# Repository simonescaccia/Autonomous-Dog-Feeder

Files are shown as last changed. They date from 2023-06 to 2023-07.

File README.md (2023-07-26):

# Autonomous-Dog-Feeder

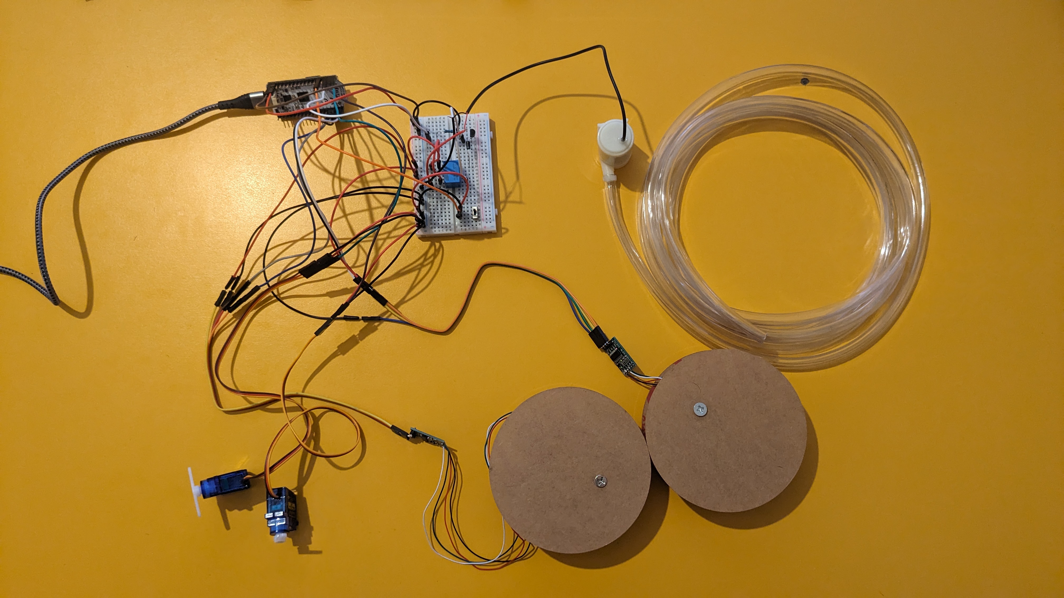
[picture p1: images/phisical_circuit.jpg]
phisical_circuit


## 1. What is the problem and why do you need IoT?

### Problems we want to solve

#### Main problem

- During the summer, some families leave their dogs because they do not have the opportunity or the desire to move with them. (formal data not found but a lot of news reports every year in the summer are released, in particular, they talk about 500 pets abandoned every day in Italy).
Duration of the holidays:  
La maggior parte sceglie di andare via tra giugno, luglio e agosto per periodi anche abbastanza lunghi: il 59% ha infatti indicato dalle 4 alle 7 notti via. Da considerare che la media 2021-2022 delle vacanze degli italiani nel periodo estivo è stata di 4 notti ([source](https://www.nostrofiglio.it/bimbi-in-viaggio/turismo-family-in-italia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,%C3%A8%20stata%20di%204%20notti.)). Then, to help dogs and families with this problem, we want to provide an autonomous dog feeder to feed the pet for at least 7 days. This project aims to build a reliable alternative to the neglect of dogs during the summer.

#### Related problems

- Dogs have a daily amount of food they need to eat, according to their age, activity level, and health condition. This amount of food is suggested by the vet or written on the dog food package. We want to make sure that the dog gets the right amount of food every day.
- Dogs need to eat their food several meals throughout the day. Each meal should be served at a specific time, according to the dog's age and activity level or preference. We want to make sure that the dog gets the right amount of food at the right time.
- Water is essential for dogs. We want to make sure that the dog has access to water at all times.
- We want to monitor the trends of the dog's eating habits and water consumption, to support the medical diagnosis.

### How we can monitor the environment?

- Food:
  - We want to measure the amount of dry food to pour in the bowl, to be able to define the amount of food for each meal. We can use a load cell sensor to measure the weight of the food.
- Water:
  - We want to measure the amount of water left in the bowl.

### Sensors

- **Load cell** sensor to measure the weight of the food in the bowl.
Periodic sensing is required to measure over time the quantity of food in the bowl.
By doing this, we can learn the dog's eating habits, like building a confidence percentage of the amount of food the dog eats at each time, to increase the power efficiency of the system.\
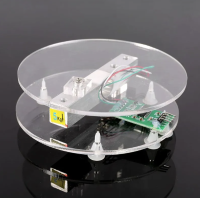
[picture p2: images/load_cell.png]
load_cell

- **Load cell** sensor to measure the weight of the water in the bowl to quantify the liters of water in the bowl (the density of the water is about 1 Kg/L, considering the temperature of the water at room temperature and the pressure at sea level).
Periodic sensing is required to measure over time the quantity of water in the bowl.
By doing this, we can learn the dog's drinking habits, like building a confidence percentage of the amount of water the dog drinks at each time, to increase the power efficiency of the system.\
load_cell
- **Slide Switch** to start or stop the autonomous dog feeder.\
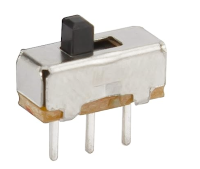
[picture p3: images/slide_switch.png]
slide_switch


### Actuators

- A **servo motor** to open and close the recipient of the food.
The activation of the servo motor will be triggered by the cloud-based service only the bowl can contain the required amount of food.\
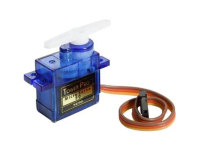
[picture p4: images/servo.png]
servo_motor

- A **servo motor** to shake the recipient of the food. The activation of the servo motor will be triggered by the cloud-based service only the bowl can contain the required amount of food.\
servo_motor
- A **water pump** fills the bowl with the water.
The activation of the water pump will be triggered by the load cell sensor only when the bowl doesn't contain the required amount of water.\
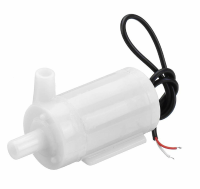
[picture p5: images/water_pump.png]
water_pump


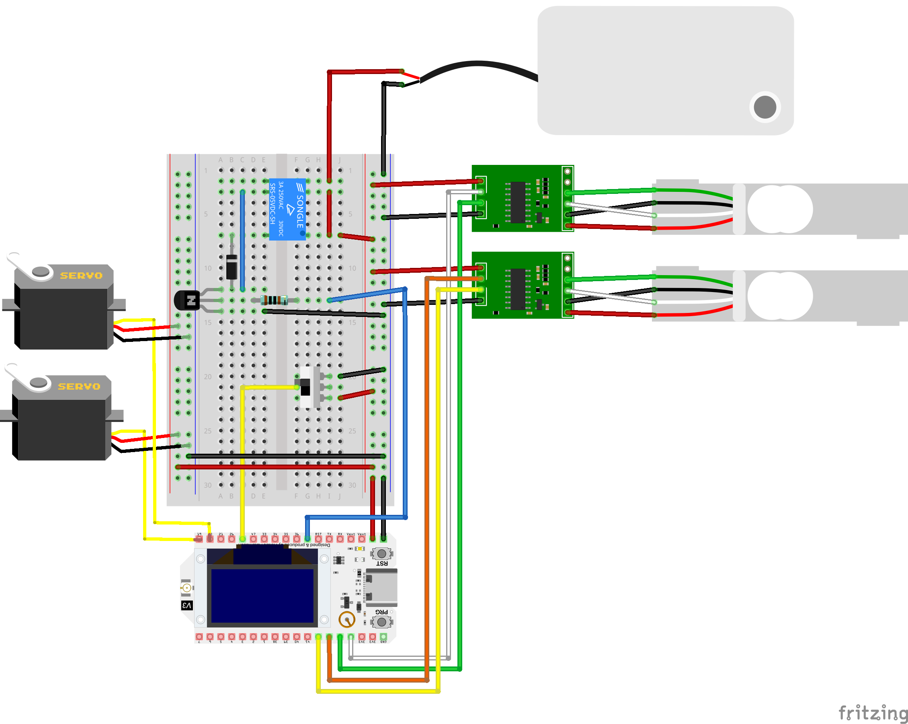
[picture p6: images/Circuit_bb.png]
circuit


## 2. What data are collected and by which sensors?

We want to collect the food and water consumption of the dog, during the day. By observing the sample data on load cells, we want to compute locally the amount of food and water consumed by the dog. Then, we want to send the computed data to the cloud-based service to store them and make them available to the dog owner.

### Sensors accuracy, the unit of measurement and periodicity

- The **load cell** sensor to measure the weight of the food in the bowl has a capacity of 5 Kg since the 1 Kg load cell is not suitable for large breeds of dogs.
Large breeds of dogs eat about 600/700 g of food per day divided into two or three meals(the amount of food is written on the dog food package). But in special cases, like pregnancy or lactation, the food quantity can be three times the normal amount. So, if a pregnant dog eats 2.1 Kg of food per day divided into two meals, a 1 Kg load cell can not be suitable for this case. More, the tare i.e. the weight of the bowl should be considered too.  
Also, we can support the fact that the resolution of the 5 Kg load cell is good enough for our purpose. The ESP32 is connected to the load cell via the HX711 amplifier, which has a resolution of 24 bits. This means that the load cell can measure the weight of the food in the bowl with a resolution of 5/2^24 = 0.0000003 Kg = 0.0003 g.
The chosen unit of measurement is grams (g) and is set using a calibration factor.
To choose the periodicity of the sensing we need to consider the fact that we are interested in monitoring the dog's eating habits, like at which time the dog starts eating considering that the food is scheduled to be served at a specific time, and the speed of eating the food in the bowl. So, to reconstruct the dog's eating velocity, we can consider that a large breeds dog finishes its meal in a maximum of 5 minutes.
Considering the sampling theorem, we need to sample every at least 2.5 minutes, but some dogs eat faster than others, in particular puppies can finish their meal in about 1 minute. So, we can choose a sampling period of 30 seconds.
This approach is a good start because we don't know a priori the eating habits of a specific dog, so we want to oversample at the beginning and then we can adjust the sampling period according to the dog's eating habits.
Finally, when the dog ends its meal we can stop the sensing until a new scheduled meal is served.
- The **load cell** sensor to measure the weight of the water in the bowl has a capacity of 5 Kg since the weight of the bowl can saturate the 1 Kg load cell.
The chosen unit of measurement is liters (L) and is set using a calibration factor since we can assume 1 Kg = 1 L.
To choose the periodicity of the sensing we need to consider the fact that we are interested in having water in the bowl at all times and monitoring the dog's water consumption habits, like how much water the dog drinks during the day.
So, to have water in the bowl at all times, we can consider that the dog drinks continuously for a maximum of 30 seconds and after that, the bowl can be empty, so we need to refill it.
Considering that we don't want that the water bowl refilled while the dog is drinking, we can choose a sampling period of 30 seconds.
  
### Collected data velocity, variability and variety

- Food data: the velocity of the data is one sample every 30 seconds, but only if the bowl is not empty and the dog has eaten something, otherwise the data is not collected (variability). The variety of data goes from the weight of a single meal, specified by the dog owner, to 0 g excluded. Peaks in the weight of the food can be caused by the dog pressing the bowl while eating.
- Water data: the velocity of the data is one sample every 30 seconds, but only if the dog has drunk something, otherwise the data is not collected (variability). The variety of data goes from the capacity of the bowl, defined by the vendor of the autonomous dog feeder, to 0 L excluded. Peaks in the weight of the water can be caused by the dog pressing the bowl while drinking.

### Data analysis

- Local data analysis: every sample is analyzed locally to check if something strange is happening, like:
  - If the weight of the food or the liters of water is negative, then we can assume there is an accuracy error in the sensor, so we can set the value to 0.
  - If the weight of the food is greater than the poured one, then we can assume that the dog is pressing the bowl while eating, so we can discard the sample.
  - If the water is greater than the poured one, then we can assume that the dog is pressing the bowl while drinking, so we can discard the sample.
  - If the servo motor is activated but the weight of the food is not increasing after a time defined by the distance between the recipient of the food and the bowl, then we can assume that the recipient of the food is empty, so we need to notify the dog owner.
  - If the water pump is activated but the weight of the water is not increasing after a time defined by the distance between the recipient of the water and the bowl, then we can assume that the recipient of the water is empty, so we need to notify the dog owner.
  - If we want to pour x grams of food, then we need to continuously monitor the weight of the food in the bowl and stop the servo motor when the weight of the food reaches x grams.
  - If we want to pour y liters of water, then we need to continuously monitor the weight of the water in the bowl and stop the water pump when the weight of the water reaches y liters.

- Collective data analysis: we expect to obtain similar habits for dogs with the same characteristics, like breed, age, weight, etc. So, we can use the data collected from all the dogs to predict the eating habits of a new dog with similar characteristics.

### Data prediction model and energy consumption

Without the data prediction model, as described above, we will monitor the water and food bowl every 30 seconds, and the energy consumption can be approximated to the following (considering that the servos and the water pump are activated only when needed, generally less than 10 times a day):

- water load cell: 0.0015 A * 5 V = 0.0075 W
- food load cell: 0.0015 A * 5 V = 0.0075 W
- water pump: 0.05 A * 5 V = 0.25 W
- servo motor: 0.19 A * 5 V = 0.95 W
- ESP32 in deep sleep: 0.0008 A * 5 V = 0.004 W

Considering that sampling using the load cell require 300 milliseconds, and the rest of the 30 seconds the ESP32 is in deep sleep, we can compute the percentage of the duty cycle for the sampling. So, using the proportion 30000:100=300:x, we can compute the duty cycle x=1%.
Finally, we can compute the energy consumption for the sampling part in a day: 
$$E_{SamplingDay} = 2 * 0.0075 W * 0.01 * 24 h = 0.0036 Wh$$
$$E_{SleepDay} = 0.004 W * 0.99 * 24 h = 0.094 Wh$$

Also, we can assume that in a day we will serve the dog 2 meals and 10 water refills, in which the single refill will require 5 seconds to complete,
so we can compute the energy consumption for the serving part in a day:
$$E_{ServingServoDay} = 2 * 0.95 W * 2 * 0.000057 h = 0.0022 Wh$$
$$E_{ServingPumpDay} = 0.25 W * 10 * 0.000057 h = 0.00014 Wh$$

Also, we need to consider the energy consumption of the ESP32 while sending data through the WiFi connection in a day. We can assume about 20 sendings in a day, 10 for the water refill and 10 for the food monitoring, 5 per meal. So, we can compute the energy consumption for the WiFi connection in a day, considering 1 second for each sending:
$$E_{WiFiDay} = 0.2 W * 20 * 0.000016 h = 0.000064 Wh$$

Finally, we can compute the total energy consumption in a day:
$$E_{TotalDay} = E_{SamplingDay} + E_{SleepDay} + E_{ServingServoDay} + E_{ServingPumpDay} + E_{WiFiDay} = 0.100004 Wh$$

Then in a week:
$$E_{TotalWeek} = 7 * E_{TotalDay} = 0.700028 Wh$$

Then in a month:
$$E_{TotalMonth} = 30 * E_{TotalDay} = 3.00012 Wh$$

Then in a year:
$$E_{TotalYear} = 365 * E_{TotalDay} = 36.50014 Wh$$

So, to choose the battery, we need 5V and then:
$$mAh = \frac{Wh}{V} = \frac{36.50014 Wh}{5 V} = 7.300028 Ah$$
Which is a reasonable battery capacity for a device like the ESP32, then we meet the requirements of at least 1 week.

With the data prediction model, we can avoid the sampling part in time in which we can predict that the dog will not eat or drink, like during the night. So, a reasonable assumption is that we avoid sampling in the 33% of the day (8 hours of sleep), and we can compute the energy consumption for the sampling part in a day:
$$E_{SamplingDayPrediction} = 2 * 0.0075 W * 0.01 * 16 h = 0.0024 Wh$$
$$E_{SleepDayDutyPrediction} = 0.004 W * 0.99 * 16 h = 0.06336 Wh$$
$$E_{SleepDayFullPrediction} = 0.004 W * 8 h = 0.032 Wh$$

Then, we can compute the energy consumption in a day:
$$E_{TotalDayPrediction} = E_{SamplingDayPrediction} + E_{SleepDayDutyPrediction} + E_{SleepDayFullPrediction} + E_{ServingServoDay} + E_{ServingPumpDay} + E_{WiFiDay} = 0.09776 Wh$$

Then in a year:
$$E_{TotalYearPrediction} = 365 * E_{TotalDayPrediction} = 35.7004 Wh$$

So, using a data prediction model, theoretically, we can reduce the energy consumption of the device by 0.8 Wh in a year, which is a percentage of 2.2%.

### Data aggregation on the edge

Federeting learning: we can use the data collected from the single dog to build a partial model, and share the parameters of the model with the cloud-based service to build a global model, using all the partial models from all the dogs.
The global model should consider the characteristics of the dog, like breed, age, weight, etc. to predict the eating habits of a new dog with similar characteristics.
With this approach, we can avoid sending the data to the cloud-based service, but only the parameters of the partial model, to preserve the privacy of the dog and minimize the energy consumption of the device; since sending only the parameters of the partial model is less energy consuming than sending the data.

### Data aggregation on the cloud

Another approach is to send the data to the cloud-based service and build the global model there. In this case, we need to consider the privacy of the dog and the greater energy consumption of the device.

## 3. What are the connected components, the protocols to connect them and the overall IoT architecture?

### Network diagram

Data are collected from the load cell sensors via the HX711 amplifier, which is connected to the ESP32. The ESP32 makes some local data computation and sends the data to an MQTT bridge via the MQTT protocol. The MQTT bridge sends this data to an AWS endpoint. This AWS endpoint implements some rules to store the data in a DynamoDB table. Finally, the data are visualized on a web page using the AWS API Gateway which triggers a Lambda function to query the DynamoDB table and return the web page. [Web site](https://6qxfwqry1k.execute-api.us-east-1.amazonaws.com/prod/autonomous-dog-feeder)

aws_architecture

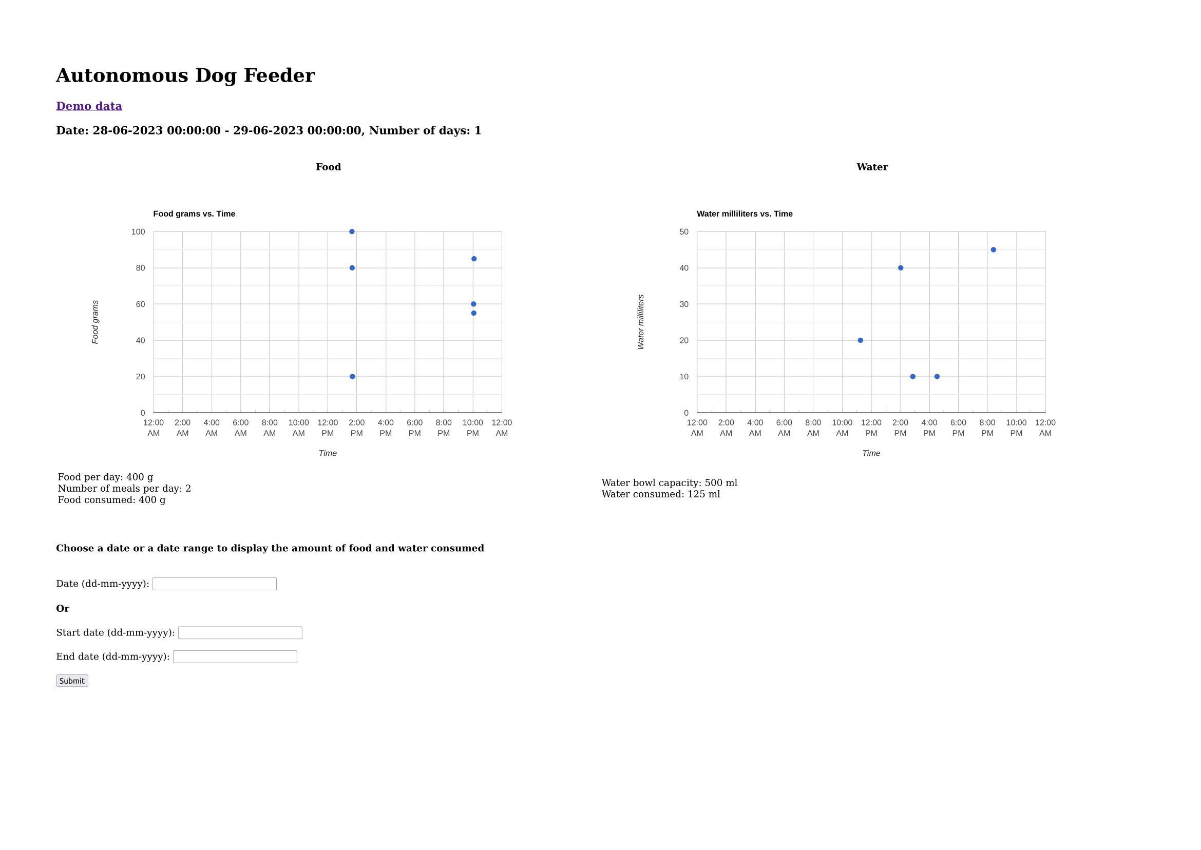
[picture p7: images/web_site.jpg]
web_site


### Software components

- Device level:
  - Food dispenser: at a given schedule, the ESP32 will shake the first servo to avoid the food getting stuck in the dispenser, then it will activate the second servo to pour the food into the bowl. The ESP32 will monitor the weight of the food in the bowl through the load cell and close the second servo when the weight of the food reaches the desired value (food per day/number of meals per day). Then the ESP32 will stop the first servo.
  - Food data computation: consider the first meal, the bowl will be filled with food, so when we sample a weight smaller than the weight of the previous sample, we can assume that the dog has eaten something, so we can compute the weight of the food eaten by subtracting the weight of the previous sample from the weight of the current sample. Then we will send this data to the cloud-based service. If the bowl is empty, then we can assume that the dog has finished its meal, so we can stop the sensing until a new scheduled meal is served.
  - Water dispenser: we want that the bowl is always filled with water at a certain level. So, at the first activation, the ESP32 will activate the water pump to fill the bowl with water and stop the water pump when the weight of the water reaches the desired value (water bowl capacity), using the load cell to monitor the weight of the water in the bowl. If the weight of the water bowl reaches a certain level (water bowl capacity/2), then the ESP32 will activate the water pump to fill the bowl with water and stop the water pump when the weight of the water reaches the desired value (water bowl capacity), using the load cell to monitor the weight of the water in the bowl.
  - Water data computation: when we sample a weight smaller than the weight of the previous sample, we can assume that the dog has drunk something, so we can compute the weight of the water drunk by subtracting the weight of the previous sample from the weight of the current sample. Then we will send this data to the cloud-based service.
- Cloud level:
  - Lambda data query: the Lambda function will query the DynamoDB table selecting the samples in a given interval of time.
  - Lambda data computation: the Lambda function will compute the sum of the food eaten and the sum of the water drunk in a given interval of time.
  - Lambda data visualization: formatting data to be visualized on a web page. Then the Lambda function will return a web page with the data computed.

### Software architecture

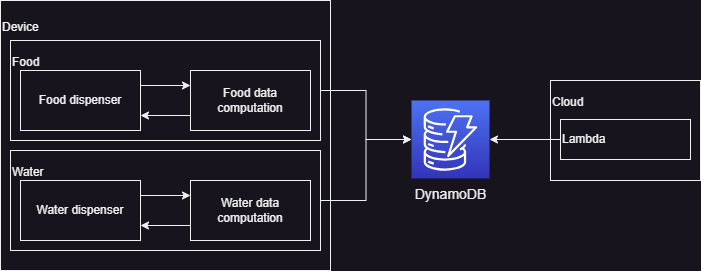
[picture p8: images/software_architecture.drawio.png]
software_architecture


## 4. How do you measure the performance of the system?

We can measure the performance of the system by comparing the data collected from the system with testing samples. These testing samples can be collected to test both the dispensed food and water but also the amount of food and water eaten and drunk by the dog.
Another metric to measure the performance of the system is the energy consumption of the device, that should satisfy the requirement.

### Aggregation on cloud

Time:

- about 400 milliseconds to sample the weight on the load cell, compute the consumption and send an MQTT message to the MQTT bridge.
- about 300 milliseconds to propagate an MQTT message to the MQTT bridge through WiFi. It depends on the WiFi protocol and on the distance between the board and the MQTT bridge. In the prototype is used an Heltec wifi-lora-32-v3, which has as WiFi protocols 802.11 b/g/n, up to 150Mbps.
- about 100 milliseconds to store the data in the DynamoDB table.
- about 400 milliseconds to compute the lambda function, to query the DynamoDB table and return the web page, in which 100 milliseconds to aggregate the data.
- total time: 1.2 seconds.

Volume:

- One message contains the deviceId and the value of the sample, so the message size is the size of two integers, which is 8 bytes. Considering that we send two messages every 30 seconds, the volume of data sent to the cloud is 16 bytes every 30 seconds, which is 32 bytes every minute, which is 1920 bytes every hour, which is 46080 bytes every day, which is 1.4 MB every month.

### Aggregation on the device

Time:

- about 400 milliseconds to sample the weight on the load cell, compute the consumption, compute the new aggrgation data (which is about 0 milliseconds since it's required only a sum) and send an MQTT message to the MQTT bridge.
- about 300 milliseconds to propagate the message to the MQTT bridge.
- about 100 milliseconds to store the data in the DynamoDB table.
- about 300 milliseconds to compute the lambda function to query the DynamoDB table and return the web page, without the aggregation of the data.
- total time: 1.1 seconds.

Volume:

- One message contains the deviceId, the value of the sample, and the aggregated data, so the message size is the size of three integers, which is 12 bytes. Considering that we send two messages every 30 seconds, the volume of data sent to the cloud is 24 bytes every 30 seconds, which is 48 bytes every minute, which is 2880 bytes every hour, which is 69120 bytes every day, which is 2.1 MB every month.

## Other resources

- [hackster.io](https://www.hackster.io/simonescaccia99/autonomous-dog-feeder-8ce118)
- [YouTube]()

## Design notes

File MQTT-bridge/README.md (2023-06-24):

# MQTT-bridge

## Documentation

[AWS mqtt client](https://github.com/aws/aws-iot-device-sdk-python/tree/master#overview)

[Paho mqtt client](https://www.eclipse.org/paho/index.php?page=clients/python/index.php)

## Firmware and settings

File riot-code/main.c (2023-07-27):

#include <stdio.h>
#include <inttypes.h>
#include <stdlib.h>
#include <string.h>

#include "fmt.h"
#include "xtimer.h"
#include "driver_hx711.h"
#include "driver_servo.h"
#include "water_pump.h"
#include "slide_switch.h"
#include "paho_mqtt_methods.h"
#include "app_params.h"

// MQTT
char* mqtt_topic_water;
char* mqtt_topic_food;

// hx711
hx711_t water_hx_dev;
hx711_t food_hx_dev;

// servo
servo_t switch_servo;
servo_t shake_servo;

// generic
bool alive = false; // switch on/off state
int32_t water_milliliters_last_refill = 0;

void init_drivers(void)
{
    // MQTT
    mqtt_topic_water = malloc(sizeof(char)*(14+strlen(board_id)+1));
    mqtt_topic_food = malloc(sizeof(char)*(13+strlen(board_id)+1));
    sprintf(mqtt_topic_water, "iot/ADF/%s/water", board_id);
    sprintf(mqtt_topic_food, "iot/ADF/%s/food", board_id);
    init_paho_mqtt();
    
    // hx711
    hx711_setup(&water_hx_dev, &water_hx711_params);
    hx711_setup(&food_hx_dev, &food_hx711_params);

    // servo
    servo_setup(&shake_servo, &shake_servo_params);
    servo_setup(&switch_servo, &switch_servo_params);

    // water_pump
    water_pump_setup();

    // slide switch
    slide_switch_setup();

}

void refill_water(void)
{
    while(hx711_get_units(&water_hx_dev) < water_bowl_milliliters)
    {
        water_pump_on();
    }
    water_pump_off();
    water_milliliters_last_refill = hx711_get_units(&water_hx_dev);
}

void compute_water_dispenser(void)
{
    int32_t water_value = hx711_get_units(&water_hx_dev); /* Sample */
    printf("water value %"PRIu32"\n", water_value);

    if(!alive) {
        // init the water bowl
        refill_water();
        return;
    }

    if (water_value < water_milliliters_last_refill) {
        // check water consumption
        publish_message(water_milliliters_last_refill - water_value, mqtt_topic_water);
        refill_water();
        return;
    }
}

int main(void)
{
    init_drivers();
    
    xtimer_ticks32_t last_wakeup;
    bool is_last_wakeup = false;

    while (1) {

        if(slide_switch_read()) {
            compute_water_dispenser();
            //compute_food_dispencer();
            alive = true;
        } else {
            alive = false;
        }

        

        //uint32_t start_time = xtimer_now_usec();

        //servo_on(&switch_servo);
        //servo_on(&shake_servo);

        //uint32_t end_time = xtimer_now_usec();
        //printf("Microseconds difference: %d\n", end_time-start_time); 
        //start_time = end_time;


        /* Duty cycle */
        if (!is_last_wakeup) {
            /* set last_wakeup only the first time */
            is_last_wakeup = true;
            last_wakeup = xtimer_now();
        }
        xtimer_periodic_wakeup(&last_wakeup, US_PER_SEC * 30);
    }

    return 0;
}

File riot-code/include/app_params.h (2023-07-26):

#ifndef APP_PARAMS_H
#define APP_PARAMS_H

#include "driver_hx711.h"
#include "servo.h"

// MQTT
#define MQTT_BRIDGE_IP "192.168.1.7"
extern const char board_id[];

// HX711
#define MAXIMUM_VALUE_LENGHT 4
extern const gpio_t water_hx_gpio_dout;
extern const gpio_t water_hx_gpio_sck;
extern const uint16_t water_hx_divider;
extern const uint8_t water_hx_read_times;
extern const hx711_gain_t water_hx_gain;
extern const hx711_params_t water_hx711_params;

extern const gpio_t food_hx_gpio_dout;
extern const gpio_t food_hx_gpio_sck;
extern const uint16_t food_hx_divider;
extern const uint8_t food_hx_read_times;
extern const hx711_gain_t food_hx_gain;
extern const hx711_params_t food_hx711_params;

// servo
#define SWITCH_SERVO_PWM_PARAM_CHAN 1
#define SHAKE_SERVO_PWM_PARAM_CHAN 0
#define SERVO_PWM_PARAM_RES 256
#define SERVO_PWM_PARAM_FREQ 100
#define SERVO_PWM_PARAM_DEV PWM_DEV(0)
#define SERVO_PARAM_MIN_US 1000UL
#define SERVO_PARAM_MAX_US 2000UL

extern const servo_pwm_params_t my_servo_pwm_params;
extern const servo_params_t switch_servo_params;
extern const servo_params_t shake_servo_params;

// water_pump
#define RELAY_PIN GPIO_PIN(0,21)

// slide switch
#define SLIDE_PIN GPIO_PIN(0,48)

// generic
extern const uint16_t water_bowl_milliliters;
extern const uint16_t daily_food_grams;
extern const uint8_t number_of_meals_per_day;

#endif

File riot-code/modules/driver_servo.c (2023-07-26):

/**
 * Define the PWM pins in boards/esp32s3-devkit/include/periph_conf.h
 * define PWM0_GPIOS  { GPIO19, GPIO20, GPIO21 } 
 * stands for PWM_DEV0
 * Channel 0: GPIO19, Channel 1: GPIO20, Channel 2: GPIO21
 * 
 * For servo 0°-90°, use:
 * #define SERVO_MIN   (1000U)
 * #define SERVO_MAX   (2000U)
 * 
 * For servo 0°-180°, use:
 * #define SERVO_MIN   (500U)
 * #define SERVO_MAX   (2500U)
 * 
 * 
*/

#include <stdio.h>
#include "driver_servo.h"

#define POS0 0
#define POS1 UINT8_MAX

void servo_setup(servo_t *dev, const servo_params_t *params)
{
    servo_init(dev, params);
}

void servo_on(servo_t *dev)
{
    servo_set(dev, POS0);
}

void servo_off(servo_t *dev)
{
    servo_set(dev, POS1);
}

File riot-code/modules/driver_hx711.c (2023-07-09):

#include <stdio.h>

#include "driver_hx711.h"
#include "periph/gpio_util.h"

/**
 * @brief Needs to wait for device to be ready while initialization
 */
static int _hx711_is_ready(hx711_t *dev)
{
    return gpio_read(dev->params.dout) == 0;
}

int32_t hx711_read(hx711_t *dev)
{
    while (!_hx711_is_ready(dev)) {}

    union {
        int32_t i32;
        struct {
            uint8_t data[3];
            uint8_t fill_byte;
        } u8;
    } value;

    value.i32 = 0;

    gpio_t sck = dev->params.sck;
    gpio_t dout = dev->params.dout;

    unsigned gain = dev->params.gain;

    value.u8.data[2] = gpio_util_shiftin(dout, sck);
    value.u8.data[1] = gpio_util_shiftin(dout, sck);
    value.u8.data[0] = gpio_util_shiftin(dout, sck);

    for (unsigned i = 0; i < gain; i++) {
        gpio_set(sck);
        gpio_clear(sck);
    }

    if (value.u8.data[2] & 0x80) {
        value.u8.fill_byte = 0xFF;
    }   
    
    return value.i32;
}

static void _hx711_set_gain(hx711_t *dev, hx711_gain_t gain)
{
    dev->params.gain = gain;
    gpio_clear(dev->params.sck);
    hx711_read(dev);
}

static void _hx711_set_offset(hx711_t *dev, int32_t offset)
{
    dev->offset = offset;
}

void hx711_init(hx711_t *dev, const hx711_params_t *params)
{
    dev->params = *params;
    dev->offset = 0;

    gpio_init(params->sck, GPIO_OUT);
    gpio_init(params->dout, GPIO_IN);

    _hx711_set_gain(dev, params->gain);
}

void hx711_setup(hx711_t *dev, const hx711_params_t *params) {
    puts("Initializing hx711");
    hx711_init(dev, params);
    hx711_power_up(dev);
    puts("Initialization successful\n\n");

    hx711_tare(dev);
}

int32_t hx711_read_average(hx711_t *dev)
{
    int32_t sum = 0;
    uint8_t i = dev->params.read_times;

    while (i--) {
        sum += hx711_read(dev);
    }

    return sum / dev->params.read_times;
}

int32_t hx711_get_value(hx711_t *dev)
{
    return hx711_read_average(dev) - dev->offset;
}


int32_t hx711_get_units(hx711_t *dev)
{
    return hx711_get_value(dev) / dev->params.divider;
}

void hx711_tare(hx711_t *dev)
{
    int32_t sum = hx711_read_average(dev);

    _hx711_set_offset(dev, sum);
}

void hx711_power_down(hx711_t *dev)
{
    gpio_clear(dev->params.sck);
    gpio_set(dev->params.sck);
}

void hx711_power_up(hx711_t *dev)
{
    gpio_clear(dev->params.sck);
}

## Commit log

2023-05-22 Inserting hx711 drivers
2023-05-22 Adding feature to hx711 driver
2023-05-25 Fixing hx711 drivers
2023-06-17 feat: inserting paho_mqtt modules
2023-06-25 Insert device id into mqtt message
2023-07-01 Inserting time prints
2023-07-02 Inserting hackster blog
    [Circuit.fzz]
2023-07-03 Update circuit
    [Circuit.fzz]
2023-07-13 Insert images
2023-07-26 Inserted new load cell device
2023-07-26 Inserting servos
2023-07-26 Inserting water pump and slide switch drivers
2023-07-27 Inserting water dispenser logic
